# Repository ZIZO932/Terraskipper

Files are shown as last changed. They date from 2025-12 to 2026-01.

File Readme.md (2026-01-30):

# Mudskipper-Inspired Soft Robot for Agriculture

## Project Description
i made this robot because i was really interested in how mudskipper fish move around in places where regular animals or even robots would just get stuck in the mud. instead of using wheels which would just spin and sink i designed this to use pectoral fins and a tail to crutch along the ground. it also has these sensors that can check the ph and tds of the soil to see if its actually a good spot to plant anything. if the soil looks okay it has this little seed planting mechanism that drops a seed which makes it a lot more useful than just a robot that walks around for no reason. it was a huge challenge to get the movement right because copying nature is way harder than it looks.

---

## Why I Made This Project
the main reason i started this was to see if i could actually take a weird movement from nature and use it for something practical like farming in muddy or salty areas. i also really wanted to get better at 3d design and electronics because i knew i would make a lot of mistakes and i wanted to see if i could fix them. this project taught me that even a tiny mistake in the 3d model like making a wall too thin can ruin the whole thing later on. it was also a big wake up call when i realized my initial sensors were for water and i had to scramble to find soil probes that wouldn't just break the second they touched the dirt.
---

## 3D Model
the 3d model was a total headache and it took so many versions to get it right. i had to make the main body hollow so it could hold all the messy wires and the pico w but it also had to be strong enough to hold the five servos. the design has these custom holders for the servos that move the fins and the tail and i also had to build a specific vertical slider for the sensors. that slider was tough because it has to push the ph and tds probes into the soil which takes a lot more force than just dipping them in water. i also had to make sure the seed planting part wouldnt jam up every time it tried to drop something.
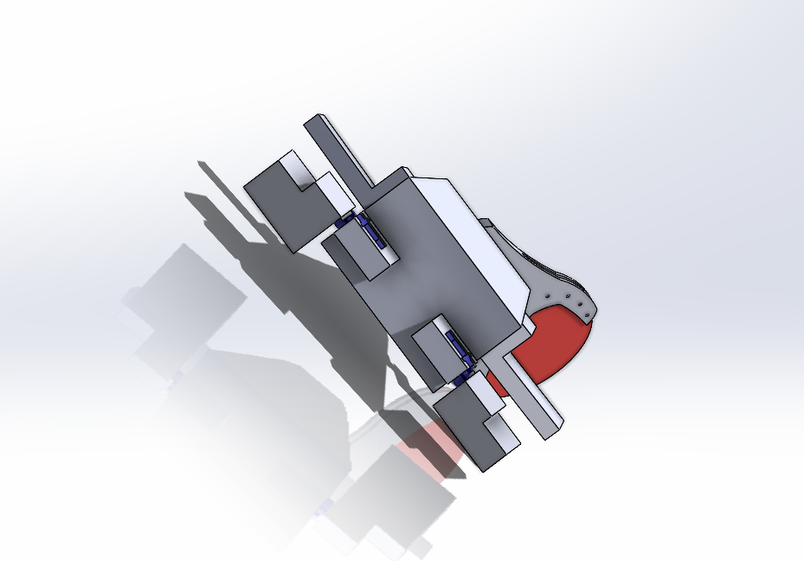
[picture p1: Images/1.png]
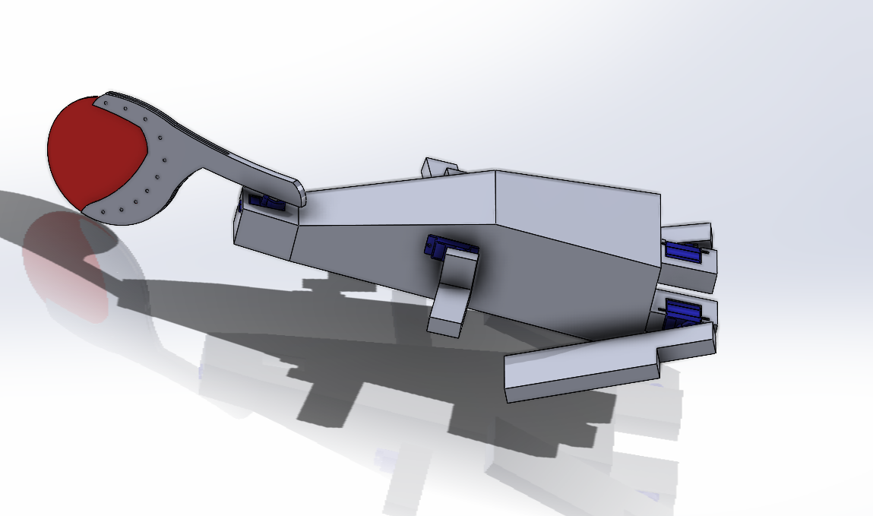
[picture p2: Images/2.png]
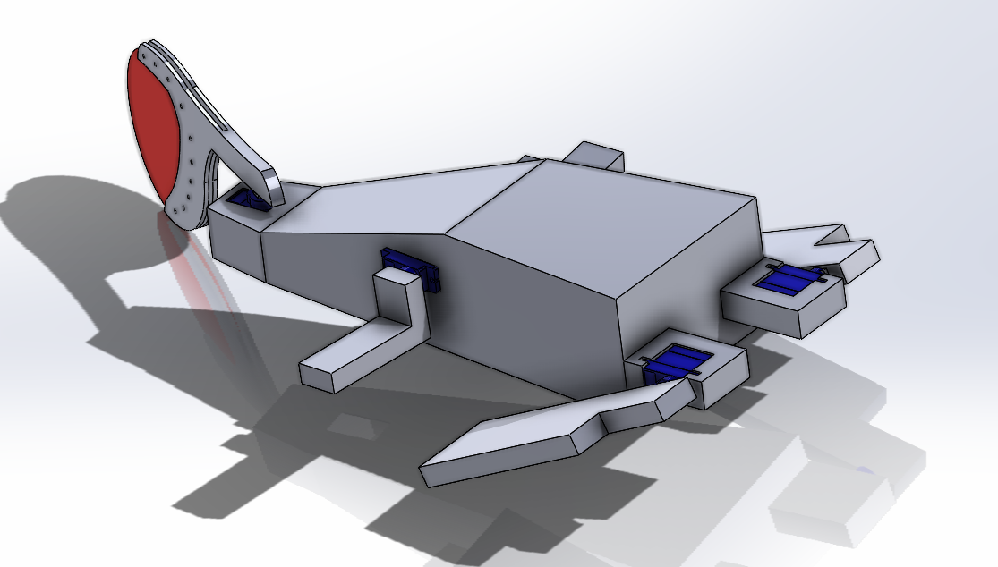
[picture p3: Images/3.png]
  

---

## Wiring Diagram
the wiring diagram was where i had to figure out how to connect everything without blowing up the pico w. it shows how the controller handles all five servos and where the data from the ph and tds sensors goes. i had to be really careful about the power because five servos pulling current at the same time can easily crash the system. i ended up using kicad to make a proper schematic and pcb because a breadboard was just becoming a nightmare of tangled wires. doing this helped me find a bunch of mistakes where i had wires crossing that would have definitely shorted out the whole thing if i hadn't caught them.
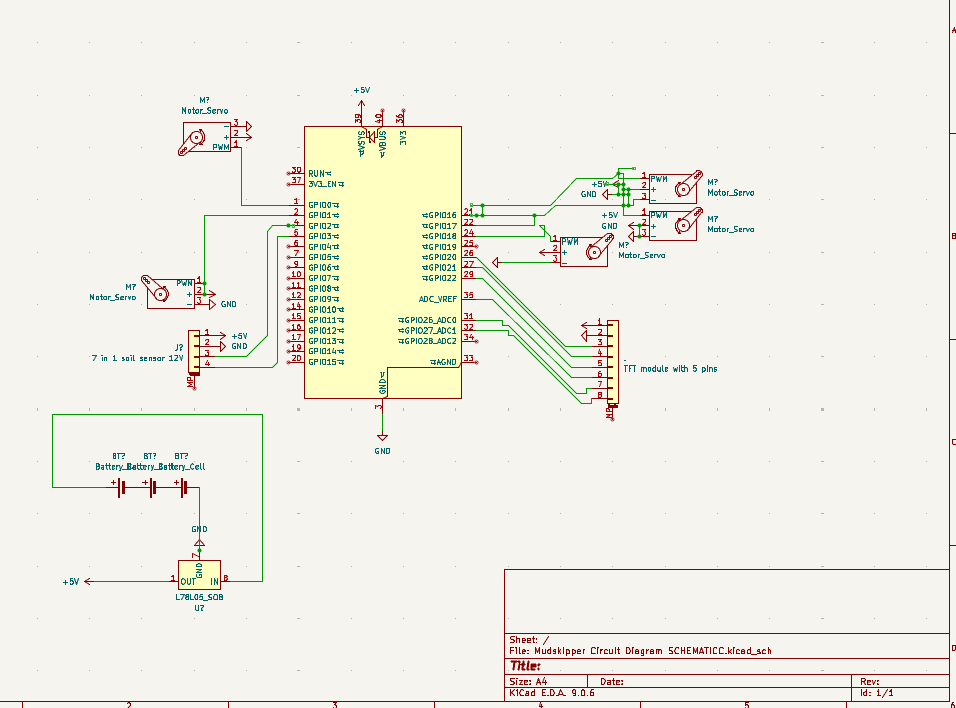
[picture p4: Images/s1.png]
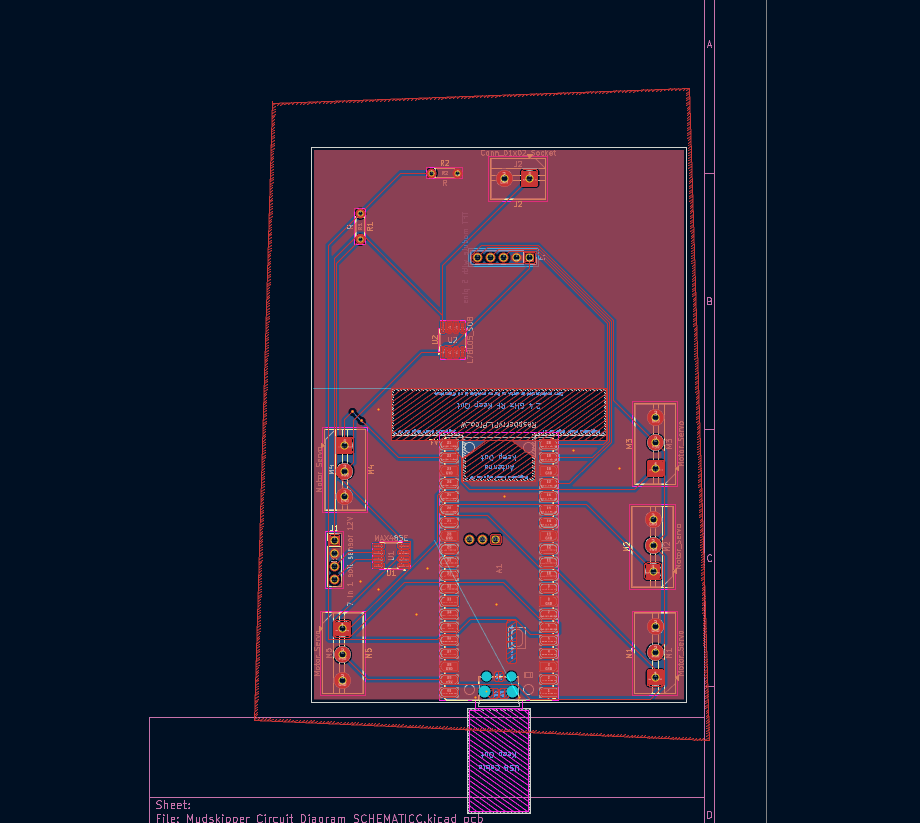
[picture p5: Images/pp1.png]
 

---

## Bill of Materials (BOM)

| Item | Description | Qty | Unit Price (EGP) | Unit Price (USD) | Total Price (USD) | URL | Running Total (USD) |
|---|---|-----|---|---|---|-----|---|
| Raspberry Pi Pico W | MCU (Main Controller) | 1 | 650 | 13.85 | 13.85 | https://electra.store/product/raspberry-pi-pico-w/ | 13.85 |
| MG996R Servo | High Torque Servo Motor | 5 | 200 | 4.26 | 21.30 | https://www.ram-e-shop.com/ar/shop/servo-mg996-180-mg996r-servo-motor-180deg-11-kg-cm-metal-gears-7397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 | 35.15 |
| 7 in 1 soil sensor | pH and TDS Measurement Sensor | 1 | 4500 | 95.87 | 95.87 | https://makerselectronics.com/product/industrial-soil-moisture-temperature-sensor-modbus-rtu-rs485/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 | 131.02 |
| Breadboard & Wires | Prototyping Accessories | 1 | 300 | 6.39 | 6.39 | https://www.ram-e-shop.com/shop/bb2t4d-j140-bb-bb-2t4d-j140-breadboard-1660-tie-point-140-jumper-wire-metal-base-6755 | 137.41 |
| XL4015 Converter | Regulation Module | 1 | 95 | 2.02 | 2.02 | https://www.ram-e-shop.com/shop/dc-dc-101-dc-dc-step-down-voltage-converter-adjustable-5a-xl4015-5v-32vdc-to-0-8v-30vdc-sku-dc101-7258 | 139.43 |
| 18650 Battery | Power Source | 2 | 245 | 5.22 | 10.44 | https://www.ram-e-shop.com/shop/battery-18650-lgcm-battery-lithium-li-ion-inr18650mh1-mh1-3200mah-10a-4-2-3-7-2-5v-rechargeable-9064 | 149.87 |
| MPU-6050 | IMU | 1 | 175 | 3.73 | 3.73 | https://www.ram-e-shop.com/shop/kit-imu-mpu6050-gy521-imu-6-dof-mpu-6050-gyroscope-accelerometer-sensor-module-7076 | 153.60 |
| NEO-6M GPS | GPS Module | 1 | 563 | 12.00 | 12.00 | https://makerselectronics.com/product/ublox-hw-539-neo-6m-gps-module/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 | 165.60 |

---

## Final Notes
this project is definitely still something i am working on and it's far from perfect. looking back i can see how much i had to change like the whole sensor mounting system and the way the fins were shaped. the mistakes i made with the 3d prints and the circuit design were actually the most useful parts of the whole experience because they forced me to learn how to troubleshoot. it might not look like a professional robot yet but it represents a lot of hours of me just trying to get a plastic fish to plant seeds in the mud.

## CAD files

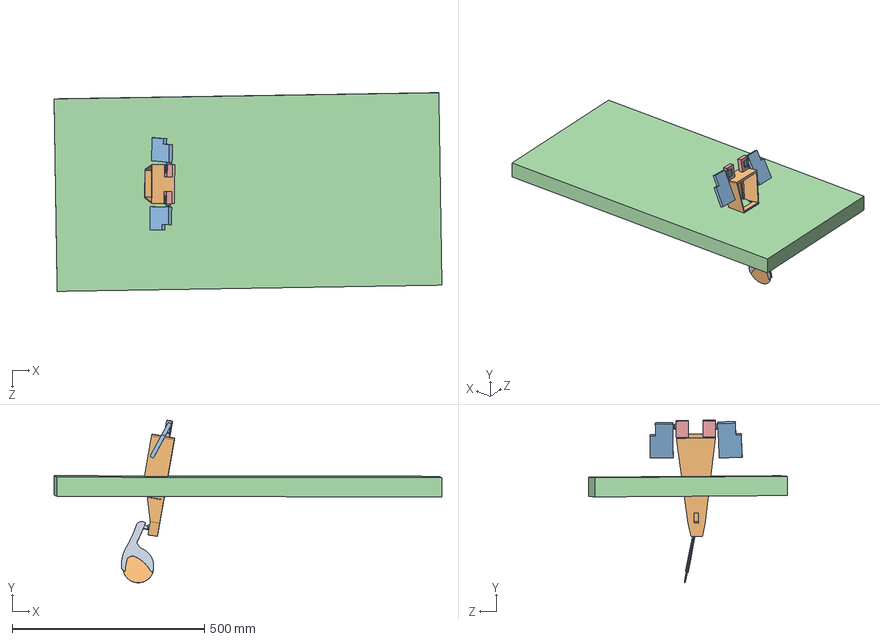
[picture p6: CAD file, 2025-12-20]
CAD/Mudskipper full.STEP
1008.0 x 422.7 x 516.5 mm
c joint
cl fin circle
pe final bigg x 2
SG90 - Micro Servo 9g - Tower Pro.1_Peça x 5
body final - Copy - Copy
senor placment x 2
floor
joint final - Copy x 2

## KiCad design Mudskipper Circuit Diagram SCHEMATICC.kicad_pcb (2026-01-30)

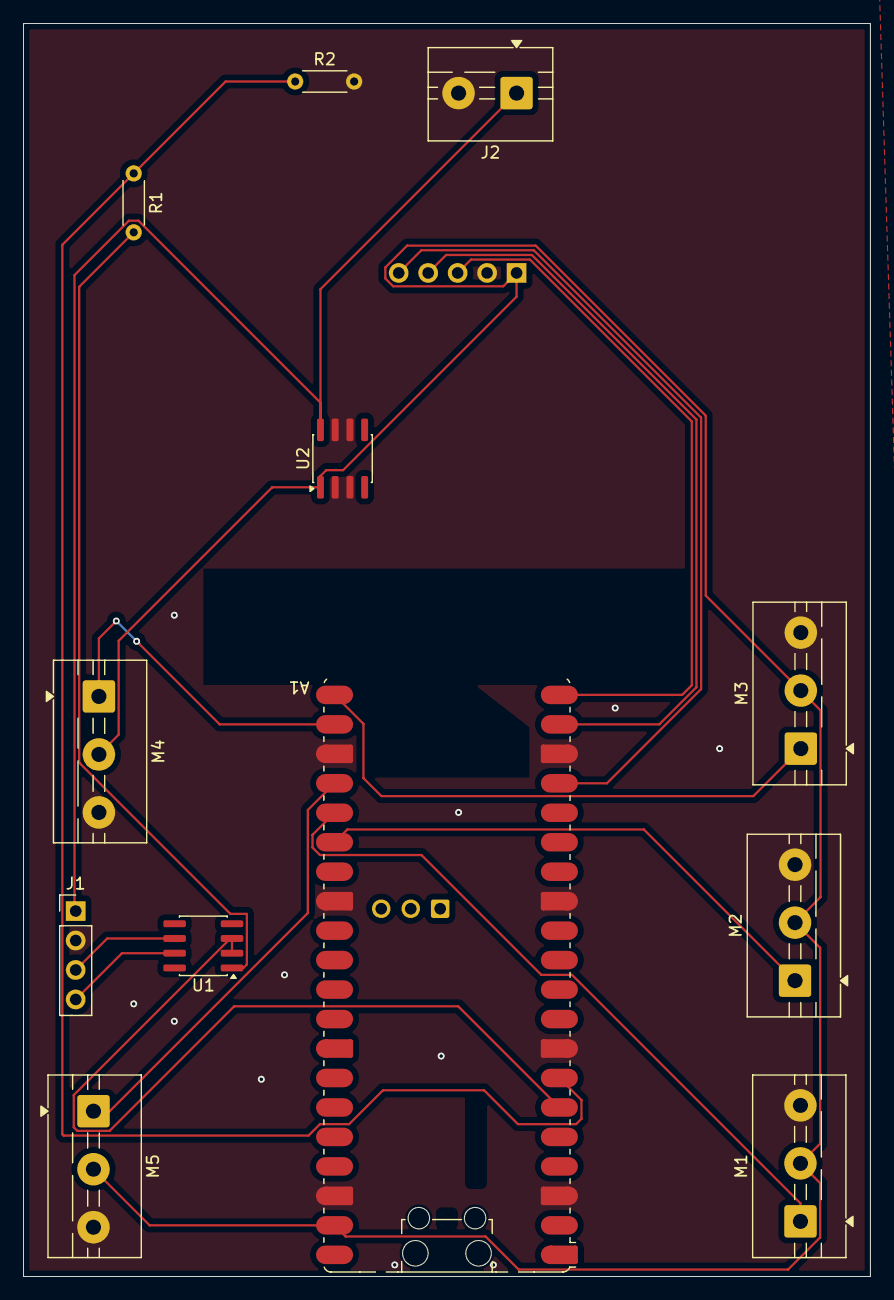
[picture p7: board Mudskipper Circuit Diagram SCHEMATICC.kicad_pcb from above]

Board: 2 copper layers, 73.0 x 108.0 mm, 13 parts (1 on the bottom side), 16 nets.

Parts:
.1: TFT module with 5 pins; PinHeader_1x05_P2.54mm_Vertical
A1: RaspberryPi_Pico_W; RaspberryPi_Pico_W_SMD_HandSolder
J1: 7 in 1 soil sensor 12V; PinHeader_1x04_P2.54mm_Vertical
J2: Conn_01x02_Socket; TerminalBlock_MaiXu_MX126-5.0-02P_1x02_P5.00mm
M1, M2, M3, M4, M5: Motor_Servo; TerminalBlock_MaiXu_MX126-5.0-03P_1x03_P5.00mm
R1, R2: R; R_Axial_DIN0204_L3.6mm_D1.6mm_P5.08mm_Horizontal
U1: MAX485E; SOIC-8_3.9x4.9mm_P1.27mm
U2: L78L05_SO8; SOIC-8_3.9x4.9mm_P1.27mm

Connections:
+5V: .1.1, A1.39 (VSYS), M1.2 (+), M2.2 (+), M3.2 (+), M4.2 (+), M5.2 (+), U2.1 (OUT)
GND: .1.2, A1.3 (GND), A1.8 (GND), A1.13 (GND), A1.18 (GND), A1.23 (GND), A1.28 (GND), A1.38 (GND), J1.2, J2.2, M1.3 (-), M2.3 (-), M3.3 (-), M4.3 (-), M5.3 (-), R2.2, U2.2 (GND), U2.3 (GND), U2.6 (GND), U2.7 (GND)
unnamed: .1.3, A1.20 (GPIO15)
unnamed: .1.4, A1.19 (GPIO14)
unnamed: .1.5, A1.17 (GPIO13)
unnamed: A1.6 (GPIO4), U1.2 (~RE), U1.3 (DE)
unnamed: A1.7 (GPIO5), R1.1, R2.1
unnamed: A1.21 (GPIO16), M3.1 (PWM)
unnamed: A1.22 (GPIO17), M4.1 (PWM)
unnamed: A1.24 (GPIO18), M5.1 (PWM)
unnamed: A1.25 (GPIO19), M1.1 (PWM)
unnamed: A1.26 (GPIO20), M2.1 (PWM)
unnamed: J1.1, J2.1, U2.8 (IN)
unnamed: J1.3, U1.6 (A)
unnamed: J1.4, U1.7 (B)
unnamed: R1.2, U1.1 (RO)

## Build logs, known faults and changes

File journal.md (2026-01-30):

# JOURNAL.md  
**Project:** Mudskipper-Inspired Soft Robot for Agriculture  
**Total Time Spent:** ~32 hours  

---

## Day 1 – Project Ideation & Research  
**Date:** Day 1  
**Time Spent:** 3 hours  

i spent about three hours just looking at videos of mudskippers because their movement is honestly kind of weird but also perfect for what i want to do. i spent a lot of time trying to figure out how they use their pectoral fins to crutch along the mud and i was wondering if i could actually replicate that with servos. the biggest struggle was honestly just trying to find actual research papers that werent too scientific but still gave me enough info on their bone structure. i started thinking about how this could actually work in a field with really salty or wet soil where a normal robot with wheels would just get stuck and die immediately. it was a bit overwhelming at first because i kept thinking if i should just make a normal walking robot but i really want to stick to the mudskipper idea.

---

## Day 2 – System Planning & Component Selection  
**Date:** Day 2  
**Time Spent:** 4 hours  

spent four hours today just trying to map out how everything is going to connect to the raspberry pi pico w. i chose that one because it has wifi and is pretty small but i started getting worried about the power draw from five different servos. i have two for the fins one for the tail and then two more just to move the sensors around which is a lot for a small board. the most annoying part was definitely the sensors because i realized that the ph and tds sensors i was looking at were actually meant for water like for a fish tank or something and that just wont work if i want to jab them into the ground. i had to spend some time looking for actual soil probes that can handle the grit and the pressure of being pushed into dirt without breaking the first time i use them.

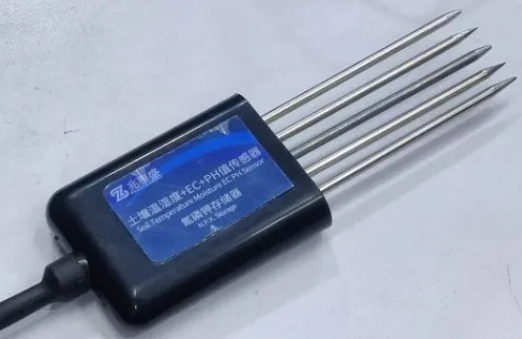
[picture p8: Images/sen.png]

---

## Day 3 – 3D Design: Main Body  
**Date:** Day 3  
**Time Spent:** 3 hours  

i started modeling the main body but the first version i made was way too thin and there was no way i was going to fit the pico and all the messy wiring inside of it. i had to go back and make the walls thicker so it wouldnt just snap but then that made the whole thing heavier which is another problem for the servos. i also struggled a lot with the alignment for the pectoral fin servos because if they are even a little bit off the robot is just going to walk in circles or flip over. i had to keep restarting the sketch because the holes for the mounting screws werent lining up with the servo brackets i found online.

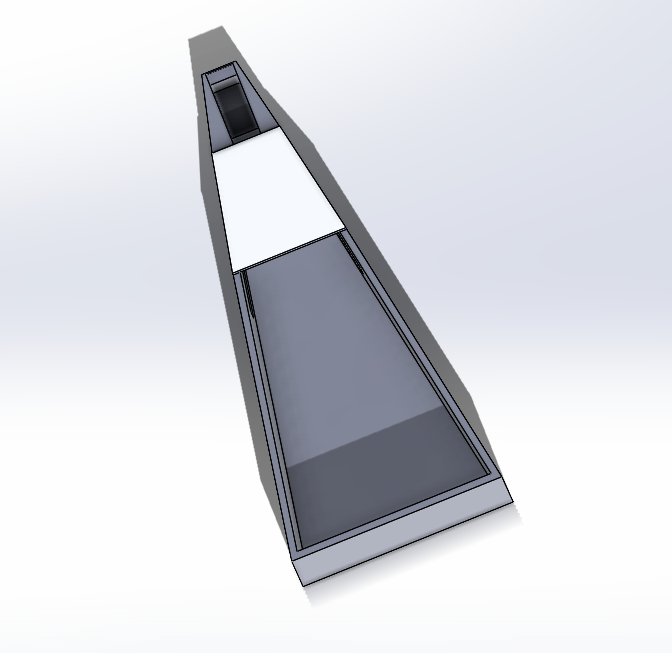
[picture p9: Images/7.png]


---

## Day 4 – Servo Holders & Structural Adjustments  
**Date:** Day 4  
**Time Spent:** 2 hours  

i spent two hours today just working on the holders that actually keep the servos in place inside the body. my first attempt was a total disaster because i didnt leave any room for the wires to come out of the side of the servo so i had to go back and chop out part of the design. it felt like i was finally getting somewhere when i got them to sit flush but then i realized i didnt leave enough clearance for the servo arm to rotate fully. i had to stay at the computer and basically carve out sections of the 3d model so the "arms" wouldnt hit the chassis. it was one of those days where you feel like you did a lot of work but you dont have much to show for it except a slightly different looking box.

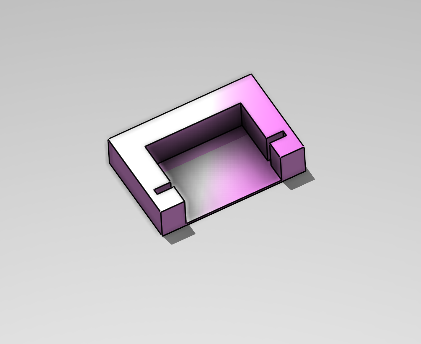
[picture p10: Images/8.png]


---

## Day 5 – Pectoral Fins (Hands of the Robot)  
**Date:** Day 5  
**Time Spent:** 3 hours  

pectoral fins hands of the robot today was all about the fins and it took me three hours to get a shape i actually liked. i wanted them to look like the broad flat fins of a real mudskipper so they have enough surface area to push off the mud. the struggle here was trying to figure out how to attach them to the plastic servo horns because if i just glue them they will definitely fall off after five minutes of walking. i had to design a little socket that the horn fits into tightly and then screw it in. i went through like three different shapes because some were too long and were bending too much and others were too short to actually lift the body up.

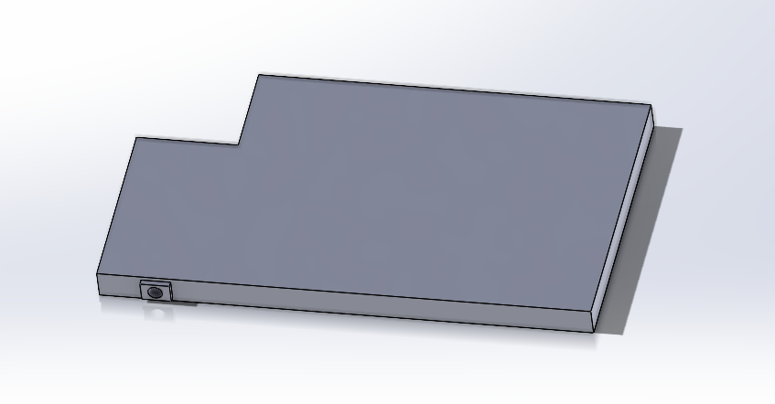
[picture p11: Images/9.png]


---

## Day 6 – Tail Design & Locomotion Concept  
**Date:** Day 6  
**Time Spent:** 3 hours  

i spent three hours on the tail today and i almost made it way too complicated. i was going to make this multi jointed tail that wagged back and forth like a real fish but when i started looking at the code i realized it was going to be a nightmare to program. i decided to simplify it down to one single servo with a flexible piece of plastic at the end. it was kind of a relief to make that decision because it saves me so much time and it also makes the robot lighter. i still struggled with the balance though because the tail is supposed to help it stay steady but if i make it too heavy it just drags behind and slows everything down.

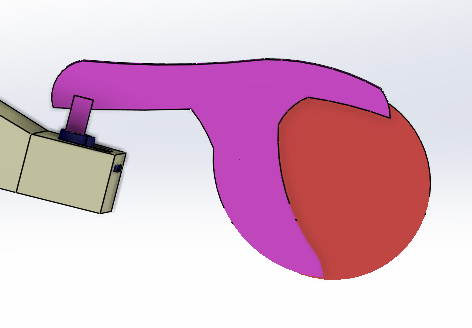
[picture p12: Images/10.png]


---

## Day 7 – Seed Planting Mechanism  
**Date:** Day 7  
**Time Spent:** 3 hours  

seed planting mechanism this was definitely the trickiest part of the whole week and i spent three hours on it. i need the robot to be able to drop seeds but only when the sensors tell it the soil is good. i made a little hopper and a channel for the seeds to slide down but they kept getting jammed in the opening because they are slightly irregular shapes. i had to rebuild the whole channel to be smoother and i added a little gate that is controlled by another servo. i spent so much time just dropping seeds through a plastic tube to see if they would get stuck. it was really tedious and honestly kind of annoying but i think i got it working now.

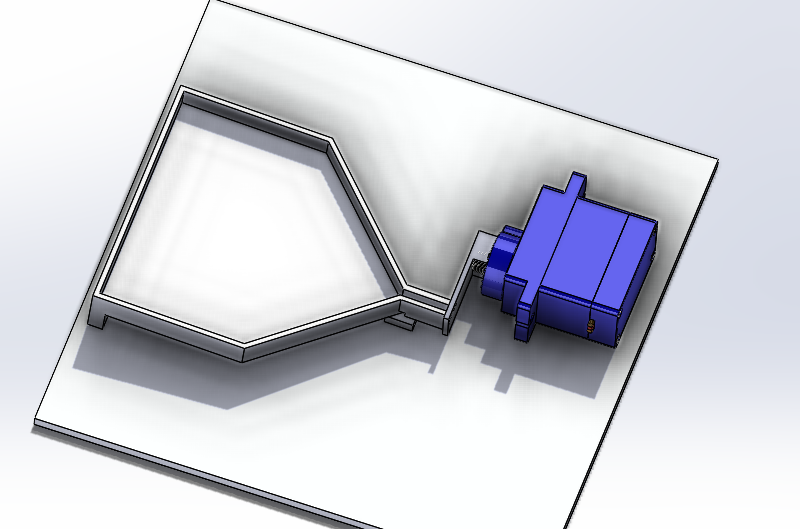
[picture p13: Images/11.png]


---

## Day 8 – Sensor Placement & Vertical Movement  
**Date:** Day 8  
**Time Spent:** 1 hours  

i spent an hour today just hacking apart the main body design again because i forgot to leave a good spot for the soil sensors. i had to make a vertical sliding system so the robot can actually push the probes into the ground to get a reading and then pull them back up so it can move. this was hard because soil is a lot tougher to poke than water so the servo has to be really strong. i had a few designs that just looked too flimsy and i knew they would snap the first time they hit a rock in the dirt. i finally came up with a rack and pinion style setup that feels a bit more solid.

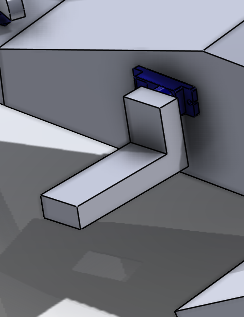
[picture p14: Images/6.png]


---

## Day 9 – Circuit Design and PCB (Kicad)  
**Date:** Day 9  
**Time Spent:** 5 hours  

today was a massive five hour grind on the electrical side and i switched over to using kicad to get everything done. mapping out the connections for five servos plus the sensors and the pico was a huge headache because the schematic kept getting so messy with lines crossing everywhere and i had to keep deleting things and starting over to make it readable. once i finally got the schematic done i moved on to the pcb layout which was even harder because i had to fit all the traces in a really tight space without causing any short circuits. i spent forever trying to figure out where to put the power traces because i really dont want the servos to pull so much current that they reset the controller or cause a brownout in the middle of a test. i also had to write some basic code just to make sure the logic pins i picked actually made sense for the pcb layout. im still a bit worried about the actual soldering part and how many wires are going to be crammed into that tiny body but at least the board design is finished and the pcb looks solid.



---

## Day 10 – Review, Reflection & Documentation  
**Date:** Day 10  
**Time Spent:** 5 hours  

today was the final stretch and i spent five hours going over everything i did for the last nine days. i looked back at the 3d models and realized just how much they changed from that first skinny version i made on day three. i spent a lot of time thinking about the sensor change too because switching from water sensors to soil probes was a huge pivot that changed the whole mechanical design of the sensor mount. 



---

## Final Reflection  
This project taught me a lot about mechanical design, electronics integration, and iterative problem-solving. Many early ideas didn’t make it into the final design, but they were essential for learning. The journal reflects not just what worked, but also what didn’t—and that’s what made the project meaningful.

**Total Logged Time:** ~32 hours
